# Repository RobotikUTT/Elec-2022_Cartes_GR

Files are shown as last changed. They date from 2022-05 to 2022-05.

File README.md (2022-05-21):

# Elec-2022_Cartes_GR

Circuits imprimés pour le Gros Robot de la Coupe de France de Robotique 2022

## PCB Arduino Mega (PCB_Mega)
Shield pour Arduino Mega 2560.
Alimentée en 5V par un bornier à vis.

**Comprends :**
- Port série pour la communication avec la Nano
- Ports séries Servos (XL320 + AX-12A)
- Sorties logiques moteurs roues
- Sorties pompes à vide
- Entrées Roues Codeuses
- Entrées analogiques courant pompes à vide
- Entrées Tirette et Interrupteur de sélection du côté
- Leds de Status Rouge, Verte et Bleue
- 10 GPIO supplémentaires non-utilisés

___

## PCB Arduino Nano (PCB_Nano)
Module hôte pour Arduino Nano.
Alimentée en 5V par un bornier à vis.

**Comprends :**
- Port série pour communication avec la Mega
- Port I2C pour écran LCD
- Entrées/Sorties Echos et Triggers pour les sonars
- 6 GPIO supplémentaires non-utilisés

## PCB Alimentation (PCB_Power)
Module d'alimentation pour le Gros Robot.

**Rails fournis :**
- 5V (2A max) : Arduinos Mega et Nano, pompes à vide et écran LCD.
- Vbat : Moteurs roues et modules Step-Down pour les Servos
(Vbat correspond à Bat+ en série avec un Fusible de 5A et le BAU)

**Comprends :**
- Connecteur arrivée de la batterie (Bat+/Bat-)
- Connecteur Bouton Arrêt d'Urgence (BAU)
- 3 sorties Vbat
- 3 sorties 5V
- 7 sorties GND (<=> Bat-)

___

## Screenshots

### PCB_Mega
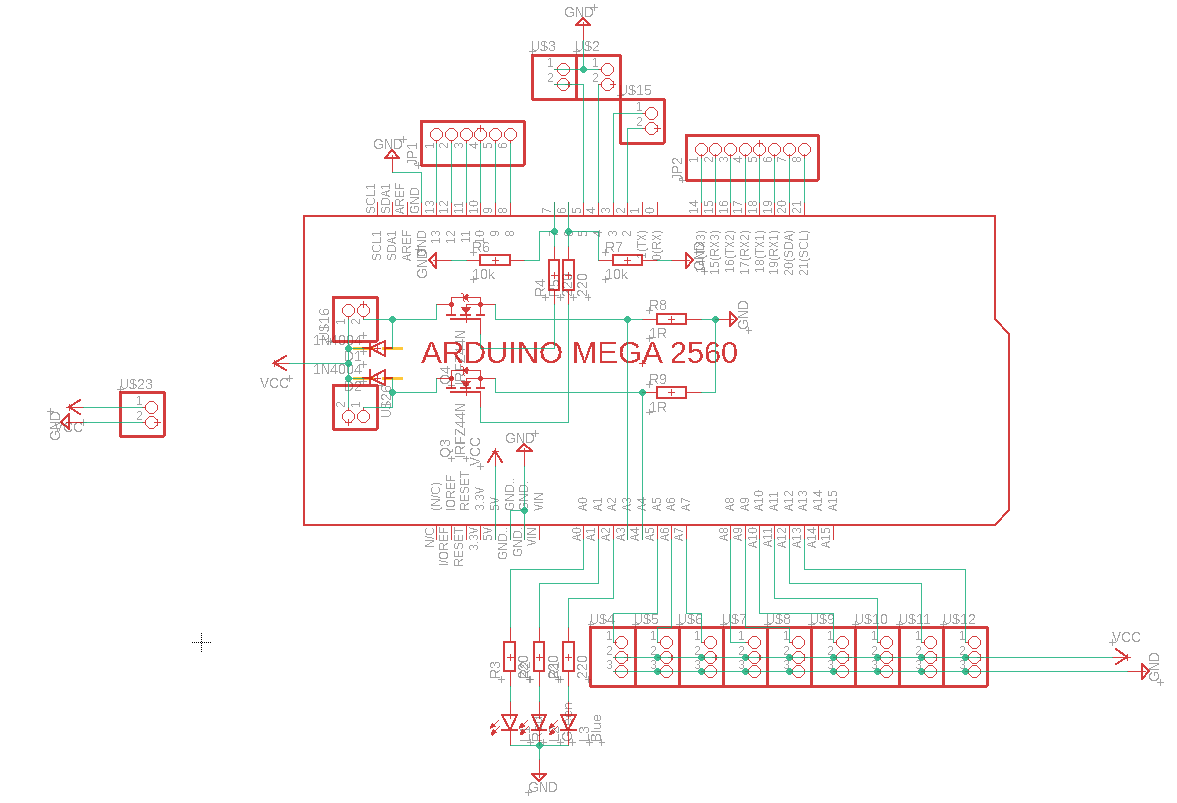
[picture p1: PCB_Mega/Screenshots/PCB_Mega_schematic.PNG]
PCB_Mega_Schematic PCB_Mega Schematic

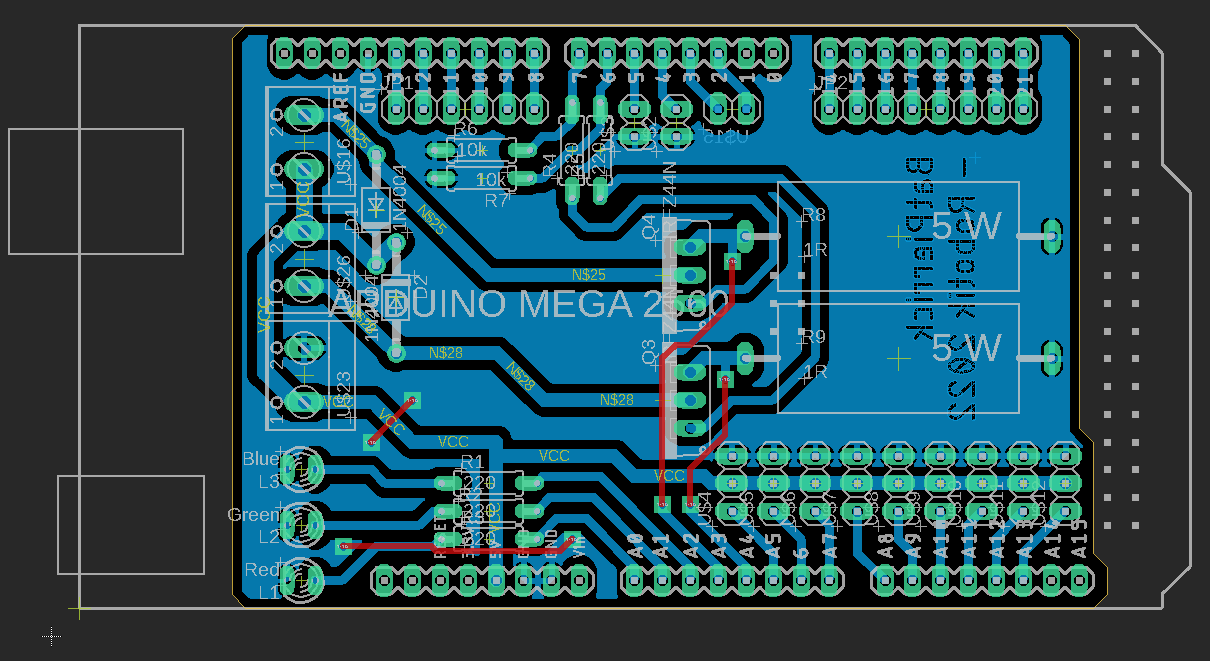
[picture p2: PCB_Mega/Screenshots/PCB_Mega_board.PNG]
PCB_Mega_Board PCB_Mega Board


### PCB_Nano
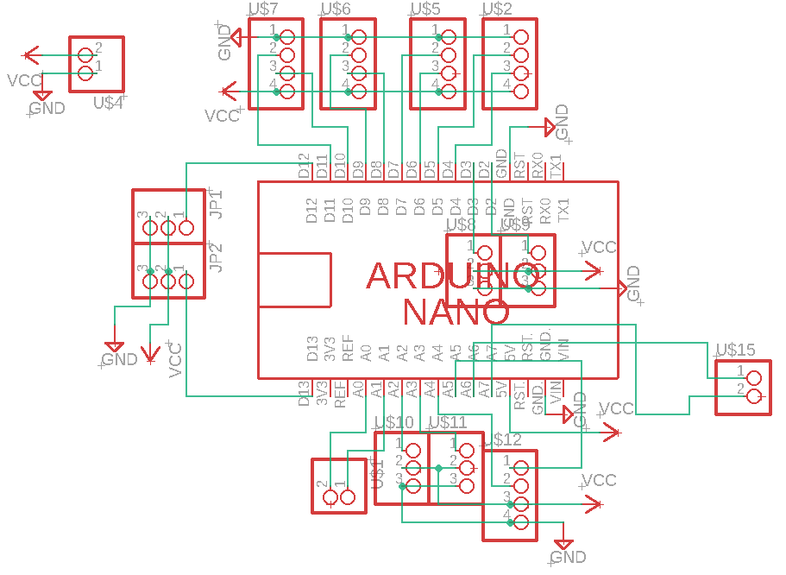
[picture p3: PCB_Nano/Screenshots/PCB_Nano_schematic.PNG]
PCB_Nano_Schematic PCB_Nano Schematic

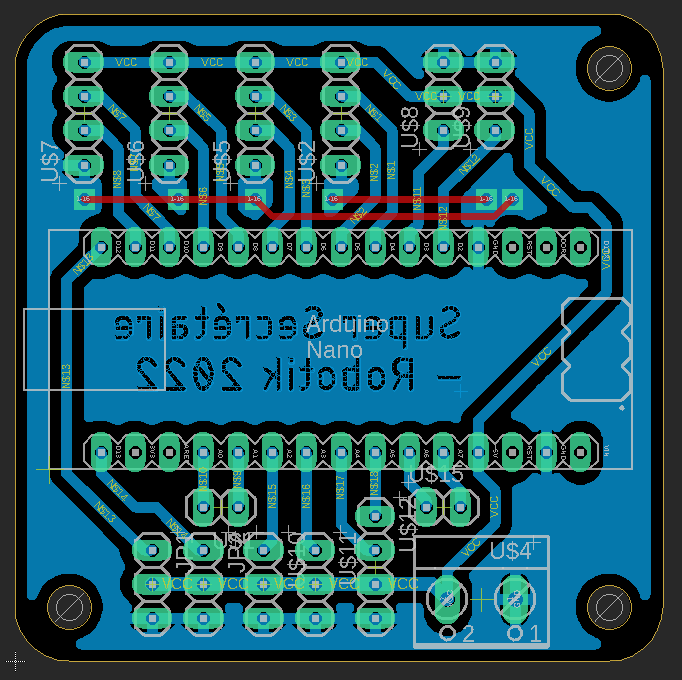
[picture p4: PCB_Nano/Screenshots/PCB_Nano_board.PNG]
PCB_Nano_Board PCB_Nano Board


### PCB_Power
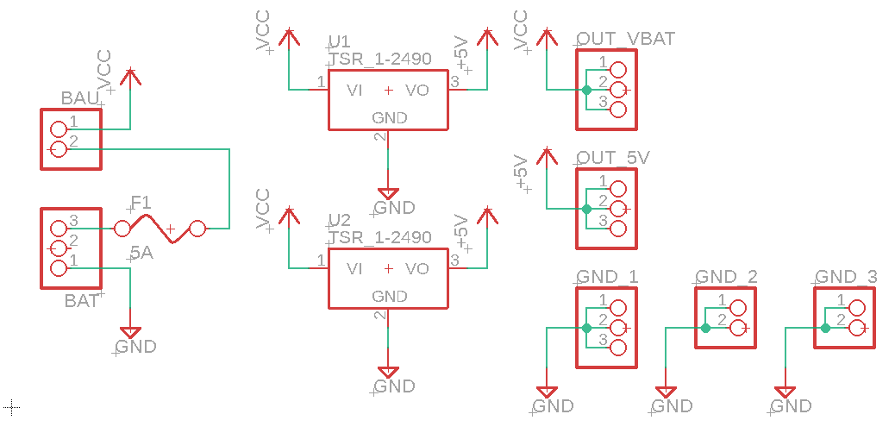
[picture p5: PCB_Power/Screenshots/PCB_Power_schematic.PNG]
PCB_Power_Schematic PCB_Power Schematic

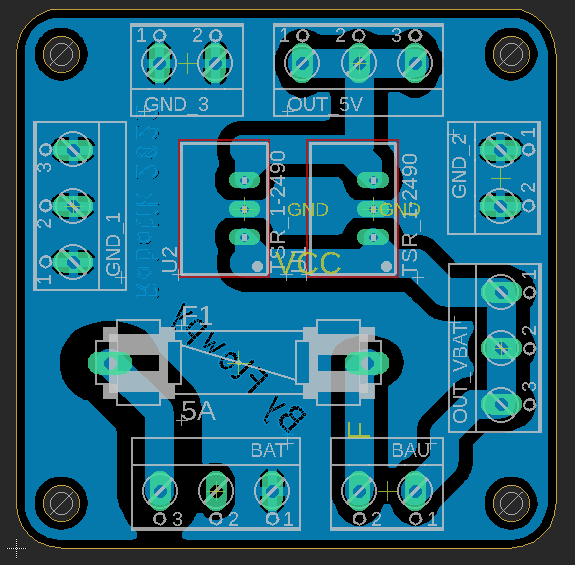
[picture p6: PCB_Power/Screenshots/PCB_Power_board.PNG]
PCB_Power_Board PCB_Power Board


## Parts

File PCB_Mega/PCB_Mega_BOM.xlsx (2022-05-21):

Composant | Quantité | Commentaire
Led 3mm Rouge | 1
Led 3mm Verte | 1
Led 3mm Bleu | 1
Bornier à vis x2 | 3
Résistance 220 ohm | 5
Résistance 10k ohm | 2
Résistance 1 ohm 5Watt | 2 | (Fourni par Flowpy à la Coupe)
Diode 1N4004 | 2
Mosfet-N IRFZ44N | 2
Pin header mâle x8 | 1
Pin header mâle x6 | 1
Pin header mâle x3 | 9
Pin header mâle x2 | 3
Pin header femelle x10 | 1
Pin header femelle x8 | 5

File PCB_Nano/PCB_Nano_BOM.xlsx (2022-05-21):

Composant | Quantité | Commentaire
Bornier à vis x2 | 1
Pin header mâle x4 | 5
Pin header mâle x3 | 6
Pin header mâle x2 | 2
Pin header femelle x15 | 2

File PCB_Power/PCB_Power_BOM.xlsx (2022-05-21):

Composant | Quantité | Commentaire
Bornier à vis x2 | 3
Bornier à vis x3 | 4
Traco TSR 1-2450 (5V 1A) | 2
Porte Fusible | 1
Fusible 5A | 1

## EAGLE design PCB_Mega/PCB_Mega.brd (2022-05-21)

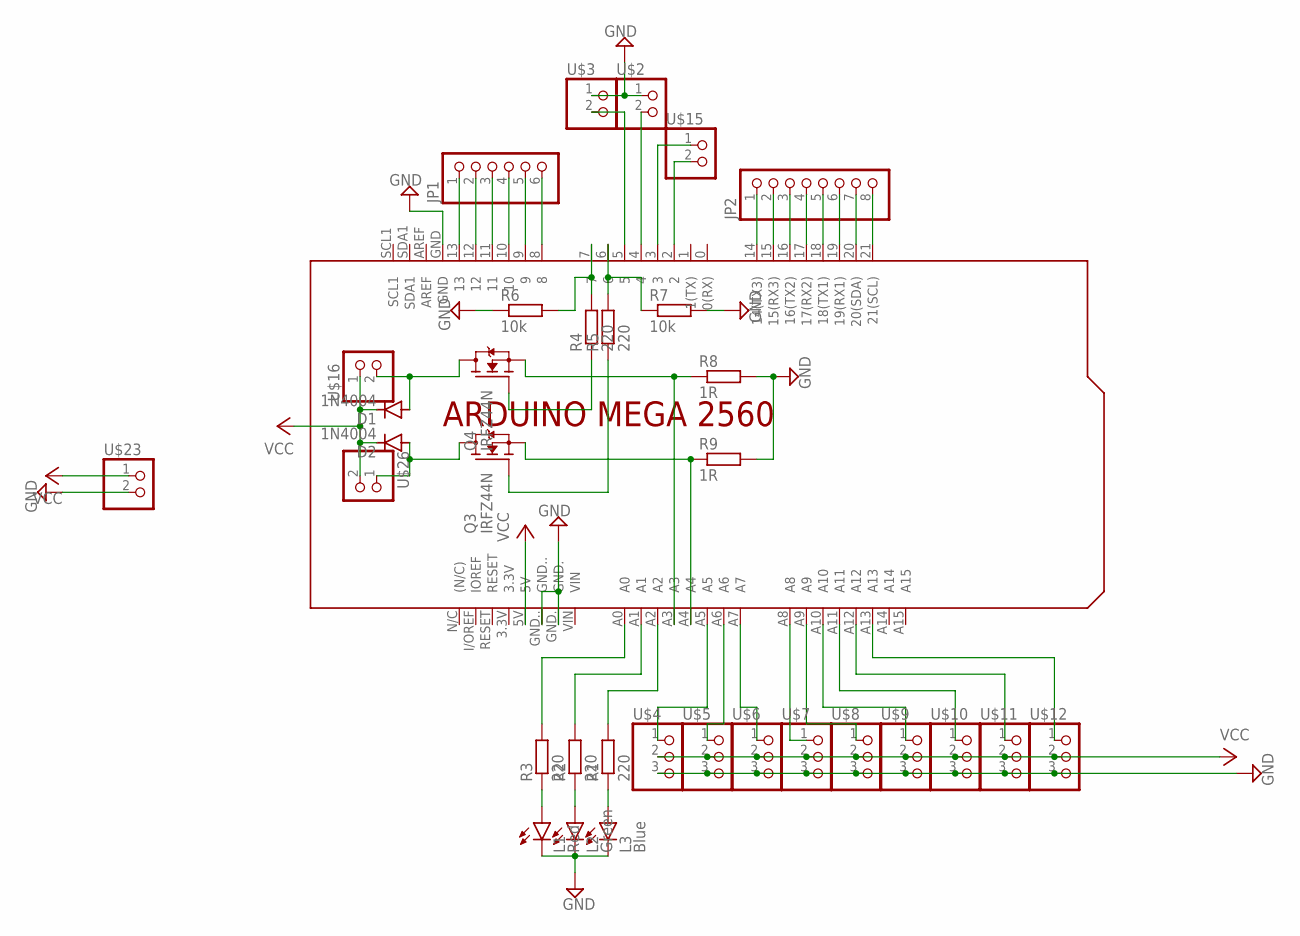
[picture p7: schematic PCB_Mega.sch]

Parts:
D1, D2: 1N4004; DO41-10
JP1: PINHD-1X6; 1X06
JP2: PINHD-1X8; 1X08
L1: Red; LED3MM
L2: Green; LED3MM
L3: Blue; LED3MM
Q3, Q4: IRFZ44N; TO220V
R1, R2, R3, R4, R5: 220; 0207/7-OFFSET
R6, R7: 10k; 0207/7-OFFSET
R8, R9: 1R; 10/28-90
U$1: ARDUINO_MEGA2560_SHIELD_NO_LOWER
U$2, U$3, U$15: PINHD-1X2; 1X02
U$4, U$5, U$6, U$7, U$8, U$9, U$10, U$11, U$12: PINHD-1X3; 1X03
U$16, U$23, U$26: TERMINALBLOCK_1X2-5.0MM

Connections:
GND: L1.K (C), L2.K (C), L3.K (C), R6.1, R7.2, R8.P$2 (2), R9.P$2 (2), U$1.GND, U$1.GND., U$1.GND.., U$2.1, U$3.1, U$4.3, U$5.3, U$6.3, U$7.3, U$8.3, U$9.3, U$10.3, U$11.3, U$12.3, U$23.2
unnamed: U$1.A5, U$4.1
unnamed: U$1.A6, U$5.1
unnamed: U$1.A7, U$6.1
unnamed: U$1.A8, U$7.1
unnamed: U$1.A9, U$8.1
unnamed: U$1.A10, U$9.1
unnamed: U$1.A11, U$10.1
unnamed: U$1.A12, U$11.1
unnamed: U$1.A13, U$12.1
unnamed: JP1.1, U$1.13
unnamed: JP1.2, U$1.12
unnamed: JP1.3, U$1.11
unnamed: JP1.4, U$1.10
unnamed: JP1.5, U$1.9
unnamed: U$1.5, U$3.2
unnamed: U$1.4, U$2.2
unnamed: JP2.1, U$1.14 (14(TX3))
unnamed: JP2.2, U$1.15 (15(RX3))
unnamed: U$1.3, U$15.1
unnamed: U$1.2, U$15.2
unnamed: JP1.6, U$1.8
unnamed: JP2.3, U$1.16 (16(TX2))
unnamed: JP2.4, U$1.17 (17(RX2))
unnamed: JP2.5, U$1.18 (18(TX1))
unnamed: D1.A, Q4.2 (D), U$16.2
unnamed: R4.2, R6.2, U$1.7
unnamed: R5.2, R7.1, U$1.6
unnamed: D2.A, Q3.2 (D), U$26.1
unnamed: JP2.6, U$1.19 (19(RX1))
unnamed: JP2.7, U$1.20 (20(SDA))
unnamed: JP2.8, U$1.21 (21(SCL))
unnamed: Q3.1 (G), R5.1
unnamed: Q4.1 (G), R4.1
unnamed: L1.A, R3.1
unnamed: L2.A, R2.1
unnamed: L3.A, R1.1
unnamed: R1.2, U$1.A2
unnamed: R2.2, U$1.A1
unnamed: R3.2, U$1.A0
unnamed: Q3.3 (S), R9.P$1 (1), U$1.A4
unnamed: Q4.3 (S), R8.P$1 (1), U$1.A3
VCC: D1.C, D2.C, U$1.5V, U$4.2, U$5.2, U$6.2, U$7.2, U$8.2, U$9.2, U$10.2, U$11.2, U$12.2, U$16.1, U$23.1, U$26.2

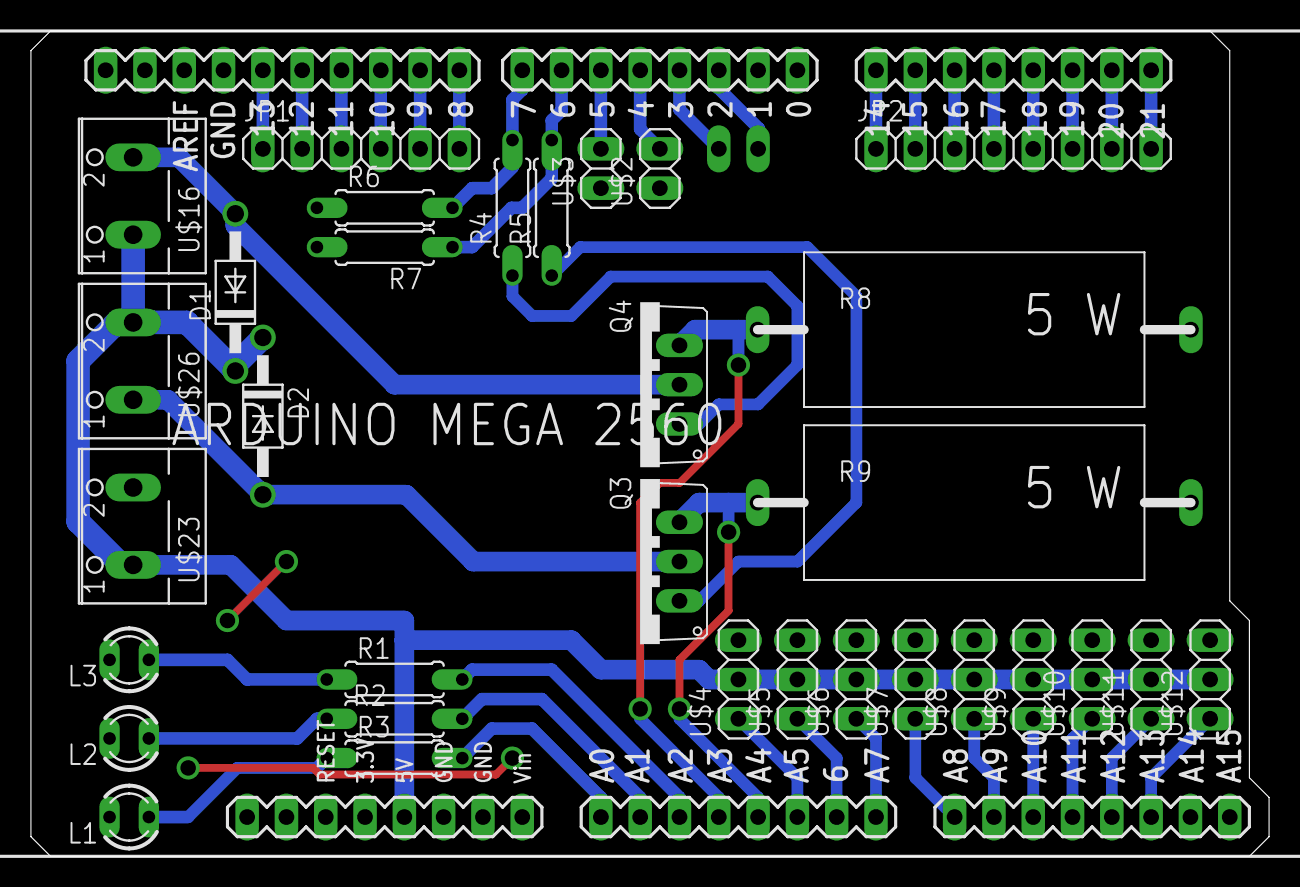
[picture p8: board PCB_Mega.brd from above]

Board: 2 copper layers, 80.0 x 53.3 mm, 34 parts (1 on the bottom side), 43 nets.

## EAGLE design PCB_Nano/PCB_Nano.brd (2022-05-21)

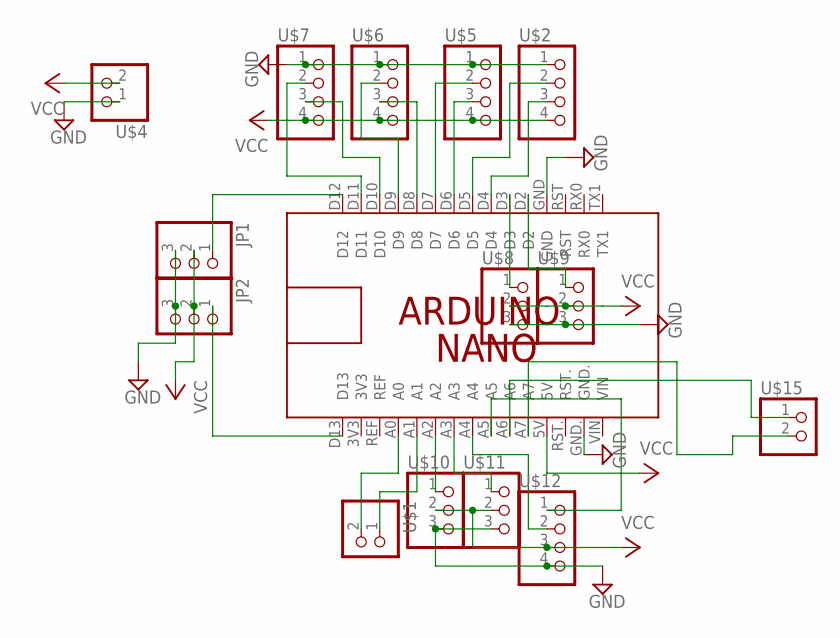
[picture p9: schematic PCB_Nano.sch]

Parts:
JP1, JP2: PINHD-1X3; 1X03
PCB1: ARDUINO_NANO_SHIELD; ARDUINO_NANO_W_HEADER_&_SOCKET
U$1, U$15: PINHD-1X2; 1X02
U$2, U$5, U$6, U$7, U$12: PINHD-1X4; 1X04
U$4: TERMINALBLOCK_1X2-5.0MM
U$8, U$9, U$10, U$11: PINHD-1X3; 1X03

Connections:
GND: JP1.3, JP2.3, PCB1.GND, PCB1.GND., U$2.1, U$4.1, U$5.1, U$6.1, U$7.1, U$8.3, U$9.3, U$10.3, U$11.3, U$12.4
unnamed: PCB1.D4, U$2.3
unnamed: PCB1.D5, U$2.2
unnamed: PCB1.D6, U$5.3
unnamed: PCB1.D7, U$5.2
unnamed: PCB1.D8, U$6.3
unnamed: PCB1.D9, U$6.2
unnamed: PCB1.D10, U$7.3
unnamed: PCB1.D11, U$7.2
unnamed: PCB1.A1, U$1.1
unnamed: PCB1.A0, U$1.2
unnamed: PCB1.D3, U$8.1
unnamed: PCB1.D2, U$9.1
unnamed: JP1.1, PCB1.D12
unnamed: JP2.1, PCB1.D13
unnamed: PCB1.A2, U$10.1
unnamed: PCB1.A3, U$11.1
unnamed: PCB1.A4, U$12.2
unnamed: PCB1.A5, U$12.1
unnamed: PCB1.A6, U$15.1
unnamed: PCB1.A7, U$15.2
VCC: JP1.2, JP2.2, PCB1.5V, U$2.4, U$4.2, U$5.4, U$6.4, U$7.4, U$8.2, U$9.2, U$10.2, U$11.2, U$12.3

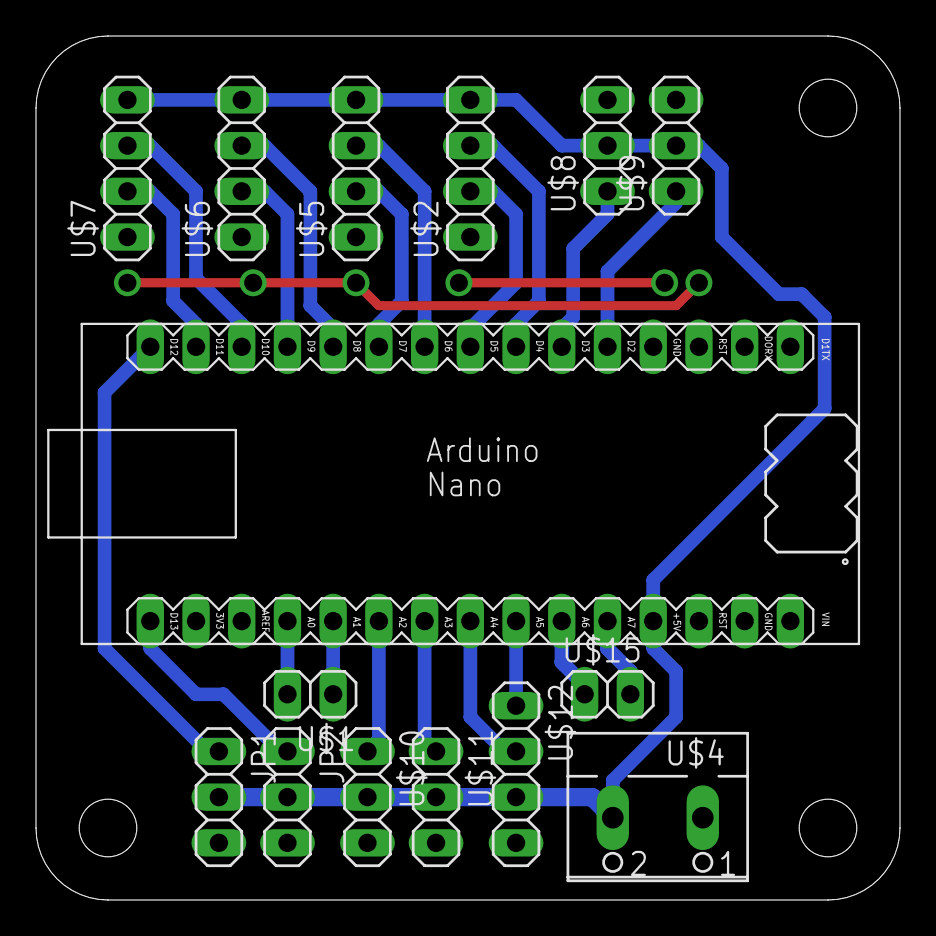
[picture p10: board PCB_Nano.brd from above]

Board: 2 copper layers, 48.0 x 48.0 mm, 15 parts (0 on the bottom side), 22 nets.

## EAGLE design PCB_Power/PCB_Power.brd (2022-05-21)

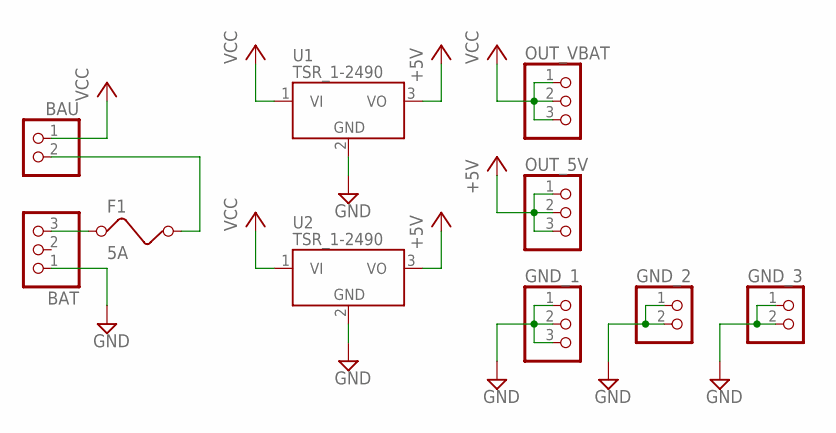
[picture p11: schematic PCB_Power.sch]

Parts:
BAT: TERMINALBLOCK_1X3-5.0MM
BAU: TERMINALBLOCK_1X2-5.0MM
F1: 5A; FUSE
GND_1: TERMINALBLOCK_1X3-5.0MM
GND_2, GND_3: TERMINALBLOCK_1X2-5.0MM
OUT_5V: TERMINALBLOCK_1X3-5.0MM
OUT_VBAT: TERMINALBLOCK_1X3-5.0MM
U1, U2: TSR_1-2490; TSR-1

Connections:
+5V: OUT_5V.1, OUT_5V.2, OUT_5V.3, U1.3 (VO), U2.3 (VO)
B_IN: BAT.3, F1.1
F: BAU.2, F1.2
GND: BAT.1, GND_1.1, GND_1.2, GND_1.3, GND_2.1, GND_2.2, GND_3.1, GND_3.2, U1.2 (GND), U2.2 (GND)
VCC: BAU.1, OUT_VBAT.1, OUT_VBAT.2, OUT_VBAT.3, U1.1 (VI), U2.1 (VI)

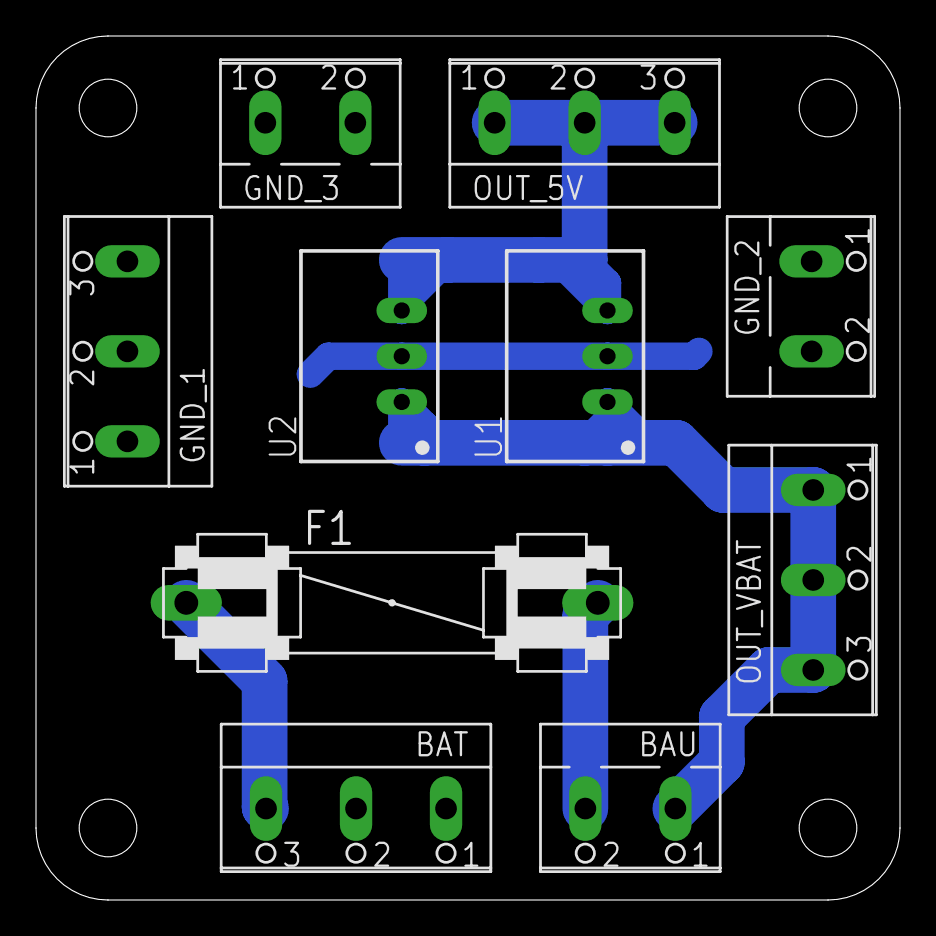
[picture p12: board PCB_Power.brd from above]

Board: 2 copper layers, 48.0 x 48.0 mm, 10 parts (0 on the bottom side), 5 nets.
